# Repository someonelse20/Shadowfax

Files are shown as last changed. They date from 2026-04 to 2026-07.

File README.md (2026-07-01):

# Shadowfax
FPV Drone designed from scrach. This design isn't fully custom yet but will get there eventually. I started this project to make a cool drone and learn as much as I can about engineering.

## Flight Controller
The meat and potatios, the main computer for the drone.
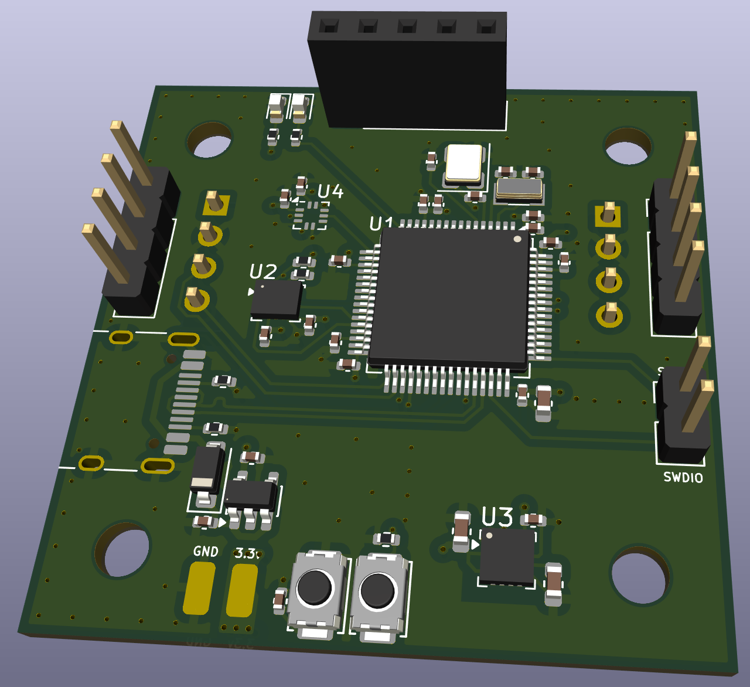
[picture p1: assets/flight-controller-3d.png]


## Transceiver
A low frequency radio to communicate with a remote controller.
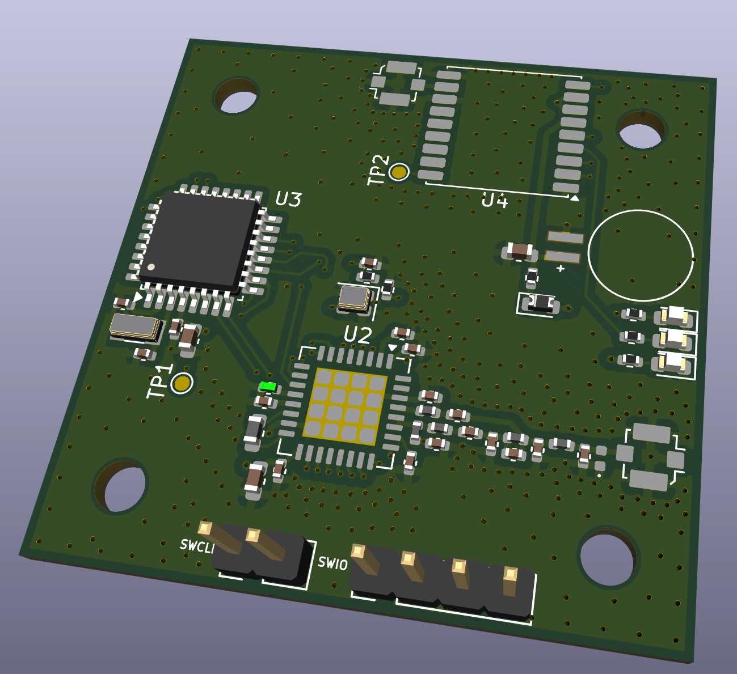
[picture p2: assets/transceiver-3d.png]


## Camera Controller
Controls the camera and captures videos and pictures with a high frequency radio for faster communication.
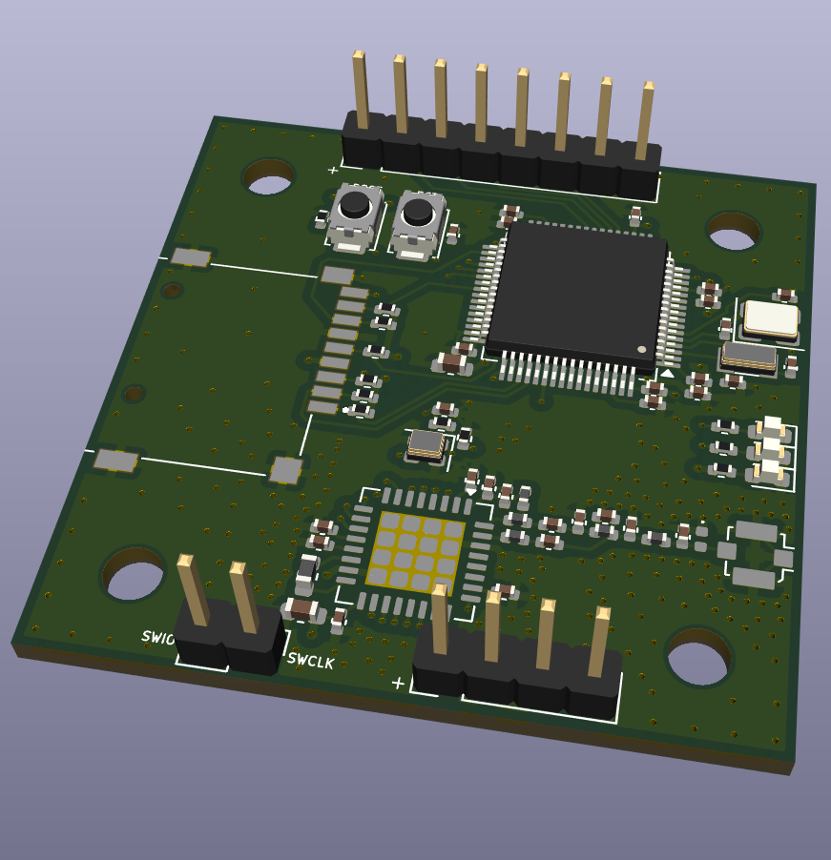
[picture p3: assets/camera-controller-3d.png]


## Power Board
Powers the whole stack with 3.3v and connects the ESCs to the input voltage.
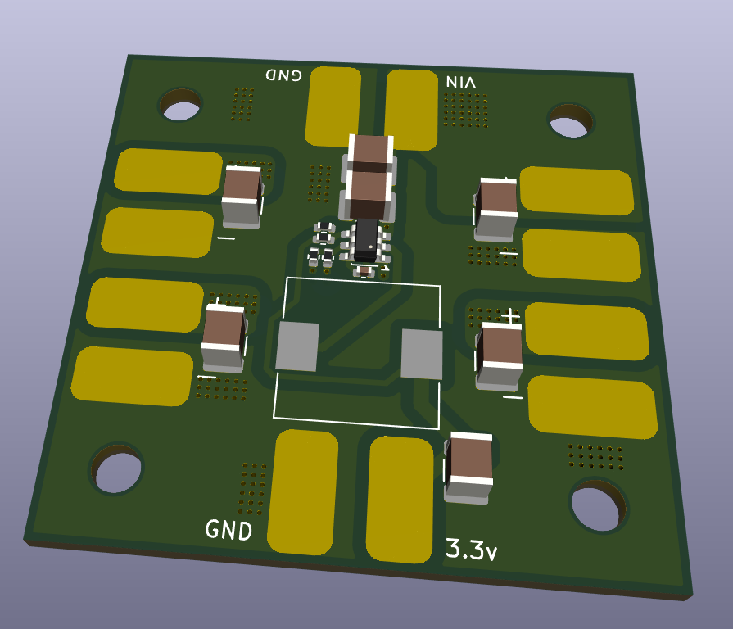
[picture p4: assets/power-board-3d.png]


## Frame
I made a custom frame to fit my custom boards and here it is.
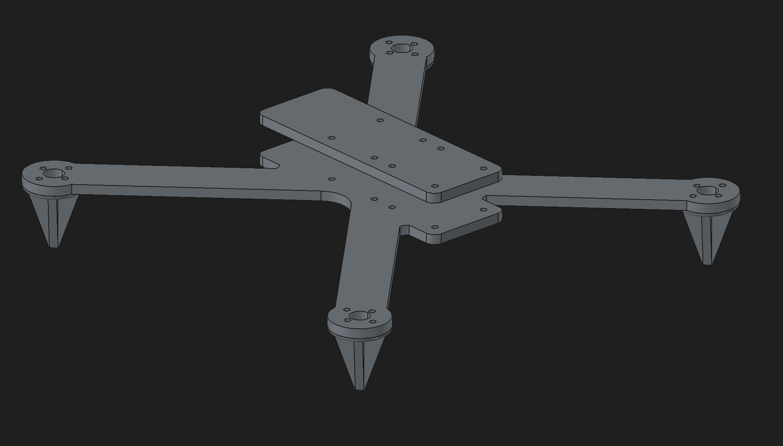
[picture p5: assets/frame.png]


## BOM
| Name | Purpose | Quantity | Total Cost (USD) | Link | Distributor |
|---|---|---|---|---|---|
| Flight Controller Assembly | Assemble components for the flight controller | 2 | 42.44 | https://jlcpcb.com | JLCPCB |
| Flight Controller Board | The pcb for the flight controller | 5 | 2.00 | https://jlcpcb.com | JLCPCB |
| Power Board Assembly | Assemble components for the power board | 2 | 14.79 | https://jlcpcb.com | JLCPCB |
| Power Board | The pcb for the power board | 5 | 7.00 | https://jlcpcb.com | JLCPCB |
| Transceiver Assmebly | Assemble components for the board | 2 | 51.31 | https://jlcpcb.com | JLCPCB |
| Transceiver Board | The pcb for the transceiver | 5 | 7.00 | https://jlcpcb.com | JLCPCB |
| Camera Controller Assembly | Assemble components for the board | 2 | 34.63 | https://jlcpcb.com | JLCPCB |
| Camera Controller Board | The pcb for the camera controller | 5 | 7.00 | https://jlcpcb.com | JLCPCB |

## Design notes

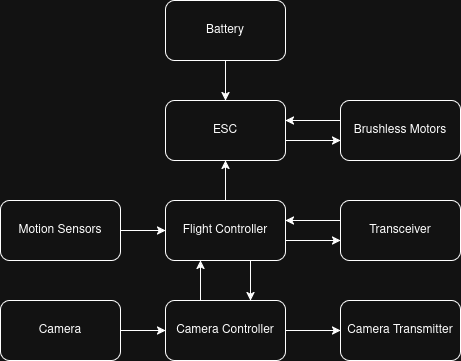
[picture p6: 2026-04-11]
Shadowfax-flowchart.png

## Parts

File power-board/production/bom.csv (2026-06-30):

Designator | Footprint | Quantity | Value | LCSC Part #
C1, C10, C12, C14, C2, C8 | 1210 | 6 | 10uF
C3 | 1210 | 1 | 47uF
C4 | 0402 | 1 | 100nF
J1, J10, J11, J12, J2, J3, J4, J5, J6, J7, J8, J9 | SolderWirePad_1x01_SMD_4x8mm | 12 | Conn_01x01
L1 | L_10.4x10.4_H4.8 | 1 | 10uH
R1, R3 | 0402 | 2 | 100K
R2 | 0402 | 1 | 22K
R4 | 0402 | 1 | 33.2K
U1 | SOT-23-6 | 1 | TPS54308

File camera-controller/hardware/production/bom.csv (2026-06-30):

Designator | Footprint | Quantity | Value | LCSC Part #
BOOT1, RESET1 | SW_Push_SPST_NO_Alps_SKRK | 2 | SW_Push
C10, C13 | 0402 | 2 | 15pF
C11, C18, C20, C24, C25, C27, C29, C31, C32 | 0402 | 9 | 100nF
C12, C14, C9 | 0402 | 3 | 18pF
C19, C21, C34, C36 | 0402 | 4 | 1uF
C2 | 0402 | 1 | 6.8pF
C26, C28, C35, C37 | 0402 | 4 | 2.2uF
C3 | 0402 | 1 | 2.7pF
C30, C33 | 0603 | 2 | 4.7uF
C38 | 0402 | 1 | 1nF
C4 | 0402 | 1 | 1.1pF
C5 | 0402 | 1 | 1.2pF
C6 | 0402 | 1 | 2pF
C7 | 0402 | 1 | 47pF
D1 | 0402 | 1 | D_TVS
D3, D4, D5 | 0603 | 3 | LED
J2 | U.FL_Molex_MCRF_73412-0110_Vertical | 1 | Conn_Coaxial
J3 | PinHeader_1x04_P2.54mm_Vertical | 1 | Conn_01x04
J4 | PinHeader_1x08_P2.54mm_Vertical | 1 | Conn_01x08
J5 | CUI_MSD-4-A | 1 | Micro_SD_Card_Det1
J6 | PinHeader_1x02_P2.54mm_Vertical | 1 | Conn_01x02
L1 | 0603 | 1 | 2.2uH
L2 | 0402 | 1 | 18nH
L3 | 0402 | 1 | 1.5nH
L4 | 0402 | 1 | 1.6nH
L5 | 0402 | 1 | 1.1nH
L7 | 0402 | 1 | 2.4nH
R10, R3, R5, R6, R7, R8, R9 | 0402 | 7 | 10K
R11, R12, R13 | 0402 | 3 | 1.2K
R4 | 0402 | 1 | 120K
TH1 | 0402 | 1 | ERT-J0ER104F
U1 | LQFP-64_10x10mm_P0.5mm | 1 | STM32H523RCTx
U2 | QFN-32-1EP_7x7mm_P0.65mm_EP4.65x4.65mm | 1 | LR2021
Y1 | Crystal_SMD_3215-2Pin_3.2x1.5mm | 1 | 32.768MHz
Y2 | Crystal_SMD_3225-4Pin_3.2x2.5mm | 1 | 24MHz
Y3 | Crystal_SMD_2016-4Pin_2.0x1.6mm | 1 | 32MHz 10pF

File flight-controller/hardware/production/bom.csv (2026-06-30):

Designator | Footprint | Quantity | Value | LCSC Part #
BOOT1, RESET1 | SW_Push_SPST_NO_Alps_SKRK | 2 | SW_Push
C1 | 0603 | 1 | 1uF
C10, C13 | 0402 | 2 | 15pF
C11, C12, C18, C20, C24, C25, C27, C29, C4, C6, C7, C8 | 0402 | 12 | 100nF
C14, C9 | 0402 | 2 | 18pF
C19, C21, C22, C23 | 0402 | 4 | 1uF
C26, C28 | 0402 | 2 | 2.2uF
C30 | 0603 | 1 | 4.7uF
C5 | 0603 | 1 | 10uF
D1, D2 | 0603 | 2 | LED
D3 | D_SOD-123 | 1 | D_Schottky
J1 | USB_C_Receptacle_HRO_TYPE-C-31-M-12 | 1 | USB_C_Receptacle_USB2.0_14P
J2, J3, J4, J5 | PinHeader_1x04_P2.54mm_Vertical | 4 | Conn_01x04
J6 | PinSocket_1x05_P2.54mm_Vertical | 1 | Conn_01x05
J7 | PinHeader_1x02_P2.54mm_Vertical | 1 | Conn_01x02
J8, J9 | SolderWirePad_1x01_SMD_1.5x3mm | 2 | Conn_01x01
R1, R2 | 0402 | 2 | 5.1K
R13, R15 | 0402 | 2 | 1K
R3 | 0402 | 1 | 10K
R4, R5 | 0402 | 2 | 1.2K
U1 | LQFP-64_10x10mm_P0.5mm | 1 | STM32H523RCTx
U2 | LGA-14_3x2.5mm_P0.5mm_LayoutBorder3x4y | 1 | LSM6DSV
U3 | LGA-16_3x3mm_P0.5mm | 1 | MMC5983MA
U4 | Rohm_MLGA010V020A_LGA-10_2x2mm_P0.45mm_LayoutBorder2x3y | 1 | BMP384
U5 | SOT-23-5 | 1 | MIC5504-3.3YM5
Y1 | Crystal_SMD_3215-2Pin_3.2x1.5mm | 1 | 32.768MHz
Y2 | Crystal_SMD_3225-4Pin_3.2x2.5mm | 1 | 24MHz

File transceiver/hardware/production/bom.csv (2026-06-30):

Designator | Footprint | Quantity | Value | LCSC Part #
BT1 | BAT_MS621FE-FL11E | 1 | MS621FE-FL11E
C10 | 0402 | 1 | 7.5pF
C11, C15 | 0402 | 2 | 1.8pF
C13 | 0402 | 1 | 18pF
C14 | 0402 | 1 | 3.9pF
C16 | 0402 | 1 | 2.2pF
C17 | 0603 | 1 | 1uF
C18, C31, C32 | 0402 | 3 | 100nF
C19, C33 | 0603 | 2 | 4.7uF
C22, C23, C8 | 0402 | 3 | 47pF
C34, C36 | 0402 | 2 | 1uF
C35, C37 | 0402 | 2 | 2.2uF
C38 | 0402 | 1 | 1nF
C9 | 0402 | 1 | 22pF
D2 | 0402 | 1 | D_TVS
D3 | 0603 | 1 | D_Schottky
D4, D5, D6 | 0603 | 3 | LED
J2, J5 | U.FL_Molex_MCRF_73412-0110_Vertical | 2 | Conn_Coaxial
J3 | PinHeader_1x04_P2.54mm_Vertical | 1 | Conn_01x04
J4 | PinHeader_1x02_P2.54mm_Vertical | 1 | Conn_01x02
L1 | 0603 | 1 | 2.2uH
L10 | 0402 | 1 | 3.9nH
L11 | 0402 | 1 | 7.5nH
L6 | 0402 | 1 | 12nH
L8 | 0402 | 1 | 4.7nH
L9 | 0402 | 1 | 24nH
R11, R12, R13 | 0402 | 3 | 1.2K
R3 | 0402 | 1 | 1K
R4 | 0402 | 1 | 120K
TH1 | 0402 | 1 | ERT-J0ER104F
TP1, TP2 | TestPoint_Pad_D1.0mm | 2 | TestPoint
U2 | QFN-32-1EP_7x7mm_P0.65mm_EP4.65x4.65mm | 1 | LR2021
U3 | LQFP-32_7x7mm_P0.8mm | 1 | STM32G030K8Tx
U4 | ublox_MAX | 1 | MAX-M10S
Y1 | Crystal_SMD_3215-2Pin_3.2x1.5mm | 1 | 32.768KHz
Y3 | Crystal_SMD_2016-4Pin_2.0x1.6mm | 1 | 32MHz 10pF

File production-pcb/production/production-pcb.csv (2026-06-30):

 | Sourced | Placed | References | Value | Footprint | Quantity
1 |  |  | C4, C6, C7, C8, C11, C12, C18, C20, C24, C25, C27, C29, C32, C40, C42, C43, C45, C46, C47, C48, C50, C53, C65, C69, C70 | 100nF | C_0402_1005Metric | 25
2 |  |  | C19, C21, C22, C23, C41, C44, C61, C63, C75, C76 | 1uF | C_0402_1005Metric | 10
3 |  |  | C26, C28, C38, C39, C58, C60, C72, C73 | 2.2uF | C_0402_1005Metric | 8
4 |  |  | C2, C3, C15, C16, C17, C31 | 10uF | C_1210_3225Metric | 6
5 |  |  | C9, C14, C34, C37, C57, C83 | 18pF | C_0402_1005Metric | 6
6 |  |  | C30, C49, C55, C66, C71 | 4.7uF | C_0603_1608Metric | 5
7 |  |  | C10, C13, C35, C36 | 15pF | C_0402_1005Metric | 4
8 |  |  | C51, C67, C68, C78 | 47pF | C_0402_1005Metric | 4
9 |  |  | C1, C74 | 1uF | C_0603_1608Metric | 2
10 |  |  | C64, C77 | 1nF | C_0402_1005Metric | 2
11 |  |  | C82, C85 | 1.8pF | C_0402_1005Metric | 2
12 |  |  | C5 | 10uF | C_0603_1608Metric | 1
13 |  |  | C33 | 47uF | C_1210_3225Metric | 1
14 |  |  | C52 | 6.8pF | C_0402_1005Metric | 1
15 |  |  | C54 | 2.7pF | C_0402_1005Metric | 1
16 |  |  | C56 | 1.1pF | C_0402_1005Metric | 1
17 |  |  | C59 | 1.2pF | C_0402_1005Metric | 1
18 |  |  | C62 | 2pF | C_0402_1005Metric | 1
19 |  |  | C79 | 22pF | C_0402_1005Metric | 1
20 |  |  | C80 | 2.2pF | C_0402_1005Metric | 1
21 |  |  | C81 | 7.5pF | C_0402_1005Metric | 1
22 |  |  | C84 | 3.9pF | C_0402_1005Metric | 1
23 |  |  | R3, R10, R11, R12, R14, R16, R17, R21 | 10K | R_0402_1005Metric | 8
24 |  |  | R4, R5, R18, R19, R20, R25, R26, R27 | 1.2K | R_0402_1005Metric | 8
25 |  |  | R13, R15, R24 | 1K | R_0402_1005Metric | 3
26 |  |  | R1, R2 | 5.1K | R_0402_1005Metric | 2
27 |  |  | R6, R8 | 100K | R_0402_1005Metric | 2
28 |  |  | R22, R23 | 120K | R_0402_1005Metric | 2
29 |  |  | R7 | 33.2K | R_0402_1005Metric | 1
30 |  |  | R9 | 22K | R_0402_1005Metric | 1
31 |  |  | L6, L8 | 2.2uH | L_0603_1608Metric | 2
32 |  |  | L1 | 10uH | L_10.4x10.4_H4.8 | 1
33 |  |  | L2 | 18nH | L_0402_1005Metric | 1
34 |  |  | L3 | 1.5nH | L_0402_1005Metric | 1
35 |  |  | L4 | 1.6nH | L_0402_1005Metric | 1
36 |  |  | L5 | 1.1nH | L_0402_1005Metric | 1
37 |  |  | L7 | 2.4nH | L_0402_1005Metric | 1
38 |  |  | L9 | 12nH | L_0402_1005Metric | 1
39 |  |  | L10 | 4.7nH | L_0402_1005Metric | 1
40 |  |  | L11 | 24nH | L_0402_1005Metric | 1
41 |  |  | L12 | 3.9nH | L_0402_1005Metric | 1
42 |  |  | L13 | 7.5nH | L_0402_1005Metric | 1
43 |  |  | D1, D2, D4, D5, D6, D9, D10, D11 | LED | LED_0603_1608Metric | 8
44 |  |  | D7, D12 | D_TVS | D_0402_1005Metric | 2
45 |  |  | D3 | D_Schottky | D_SOD-123 | 1
46 |  |  | D8 | D_Schottky | D_0603_1608Metric | 1
47 |  |  | U1, U7 | STM32H523RCTx | LQFP-64_10x10mm_P0.5mm | 2
48 |  |  | U8, U11 | LR2021 | QFN-32-1EP_7x7mm_P0.65mm_EP4.65x4.65mm | 2
49 |  |  | U2 | LSM6DSV | LGA-14_3x2.5mm_P0.5mm_LayoutBorder3x4y | 1
50 |  |  | U3 | MMC5983MA | LGA-16_3x3mm_P0.5mm | 1
51 |  |  | U4 | BMP384 | Rohm_MLGA010V020A_LGA-10_2x2mm_P0.45mm_LayoutBorder2x3y | 1
52 |  |  | U5 | MIC5504-3.3YM5 | SOT-23-5 | 1
53 |  |  | U6 | TPS54308 | SOT-23-6 | 1
54 |  |  | U9 | STM32G030K8Tx | LQFP-32_7x7mm_P0.8mm | 1
55 |  |  | U10 | MAX-M10S | ublox_MAX | 1
56 |  |  | Y1, Y3 | 32.768MHz | Crystal_SMD_3215-2Pin_3.2x1.5mm | 2
57 |  |  | Y2, Y4 | 24MHz | Crystal_SMD_3225-4Pin_3.2x2.5mm | 2
58 |  |  | Y5, Y7 | 32MHz 10pF | Crystal_SMD_2016-4Pin_2.0x1.6mm | 2
59 |  |  | Y6 | 32.768KHz | Crystal_SMD_3215-2Pin_3.2x1.5mm | 1
60 |  |  | BOOT1, BOOT2, RESET1, RESET2 | SW_Push | SW_Push_SPST_NO_Alps_SKRK | 4
61 |  |  | TH1, TH2 | ERT-J0ER104F | R_0402_1005Metric | 2
62 |  |  | TP1, TP2 | TestPoint | TestPoint_Pad_D1.0mm | 2
63 |  |  | BT1 | MS621FE-FL11E | BAT_MS621FE-FL11E | 1
64 |  |  | J10, J11, J12, J13, J14, J15, J16, J17, J18, J19, J20, J21 | Conn_01x01 | SolderWirePad_1x01_SMD_4x8mm | 12
65 |  |  | J2, J3, J5, J22 | Conn_01x04 | PinHeader_1x04_P2.54mm_Vertical | 4
66 |  |  | J4, J7, J24 | Conn_01x02 | PinHeader_1x02_P2.54mm_Vertical | 3
67 |  |  | J26, J29, J30 | Conn_Coaxial | U.FL_Molex_MCRF_73412-0110_Vertical | 3
68 |  |  | J8, J9 | Conn_01x01 | SolderWirePad_1x01_SMD_1.5x3mm | 2
69 |  |  | J1 | USB_C_Receptacle_USB2.0_14P | USB_C_Receptacle_HRO_TYPE-C-31-M-12 | 1
70 |  |  | J6 | Conn_01x05 | PinSocket_1x05_P2.54mm_Vertical | 1
71 |  |  | J23 | Conn_01x08 | PinHeader_1x08_P2.54mm_Vertical | 1
72 |  |  | J25 | Micro_SD_Card_Det1 | CUI_MSD-4-A | 1

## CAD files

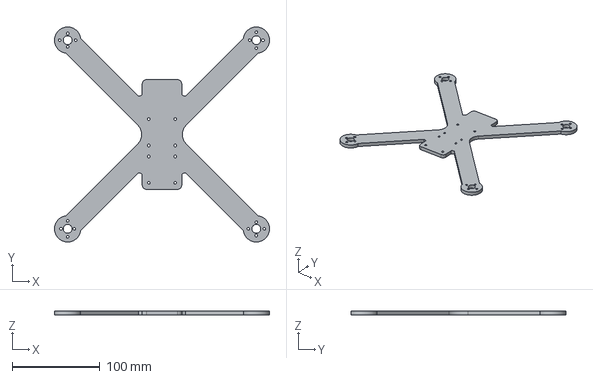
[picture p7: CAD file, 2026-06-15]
frame/exports/frame-Body.step
244.7 x 244.7 x 5.00 mm

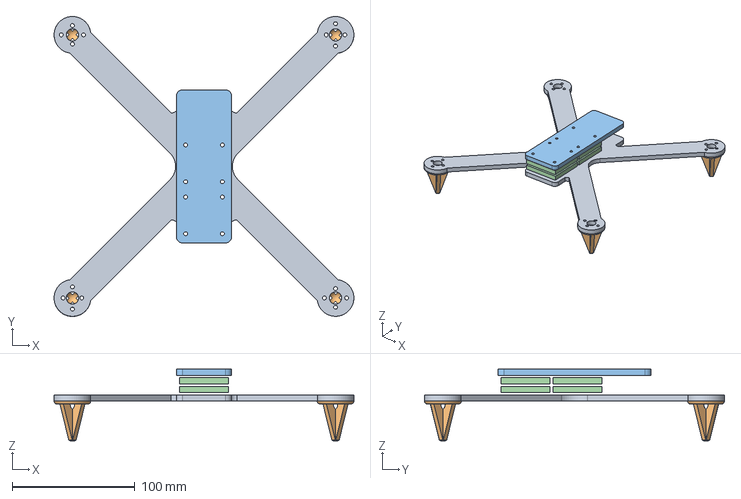
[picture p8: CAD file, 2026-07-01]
model.step
244.7 x 244.8 x 58.5 mm

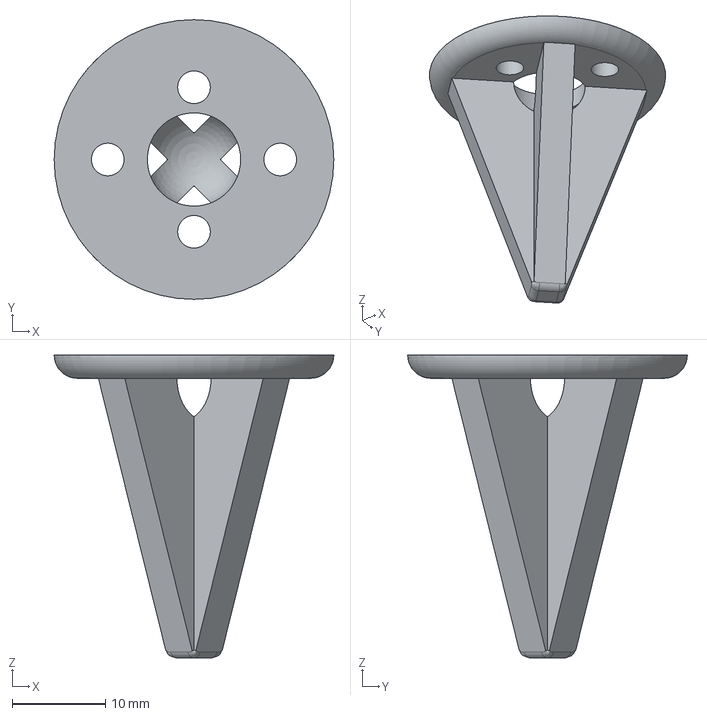
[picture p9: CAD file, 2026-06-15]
frame/exports/feet-Body.step
30.0 x 30.0 x 32.5 mm

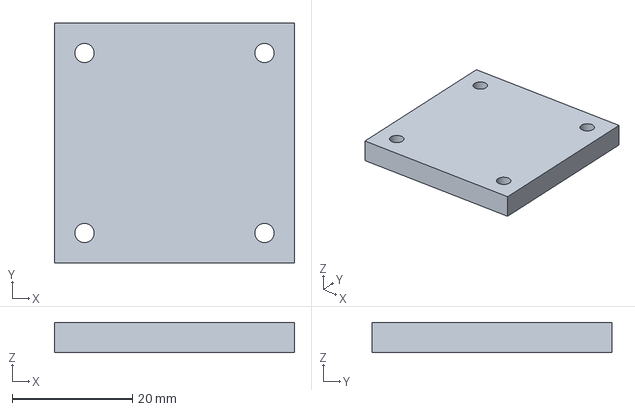
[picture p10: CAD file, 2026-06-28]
frame/board_model.FCStd
40.0 x 40.0 x 5.00 mm

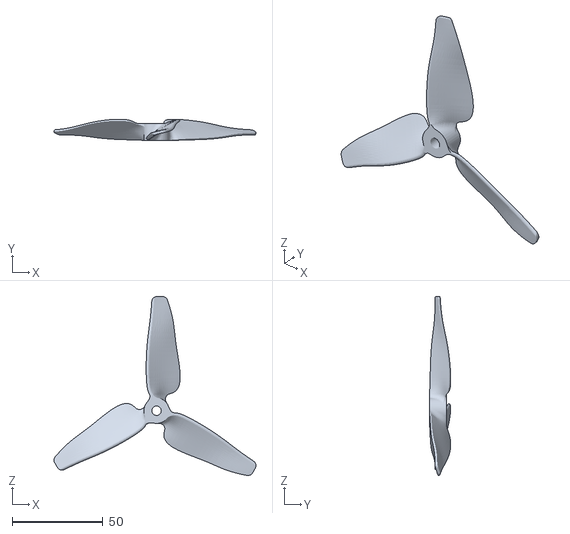
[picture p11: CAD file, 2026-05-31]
frame/Propeller_5_inch (1).stl
111.4 x 11.8 x 98.7

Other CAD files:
frame/assembly.FCStd
frame/feet.FCStd
frame/frame.FCStd
frame/sketch.FCStd
frame/exports/feet-Body.3mf

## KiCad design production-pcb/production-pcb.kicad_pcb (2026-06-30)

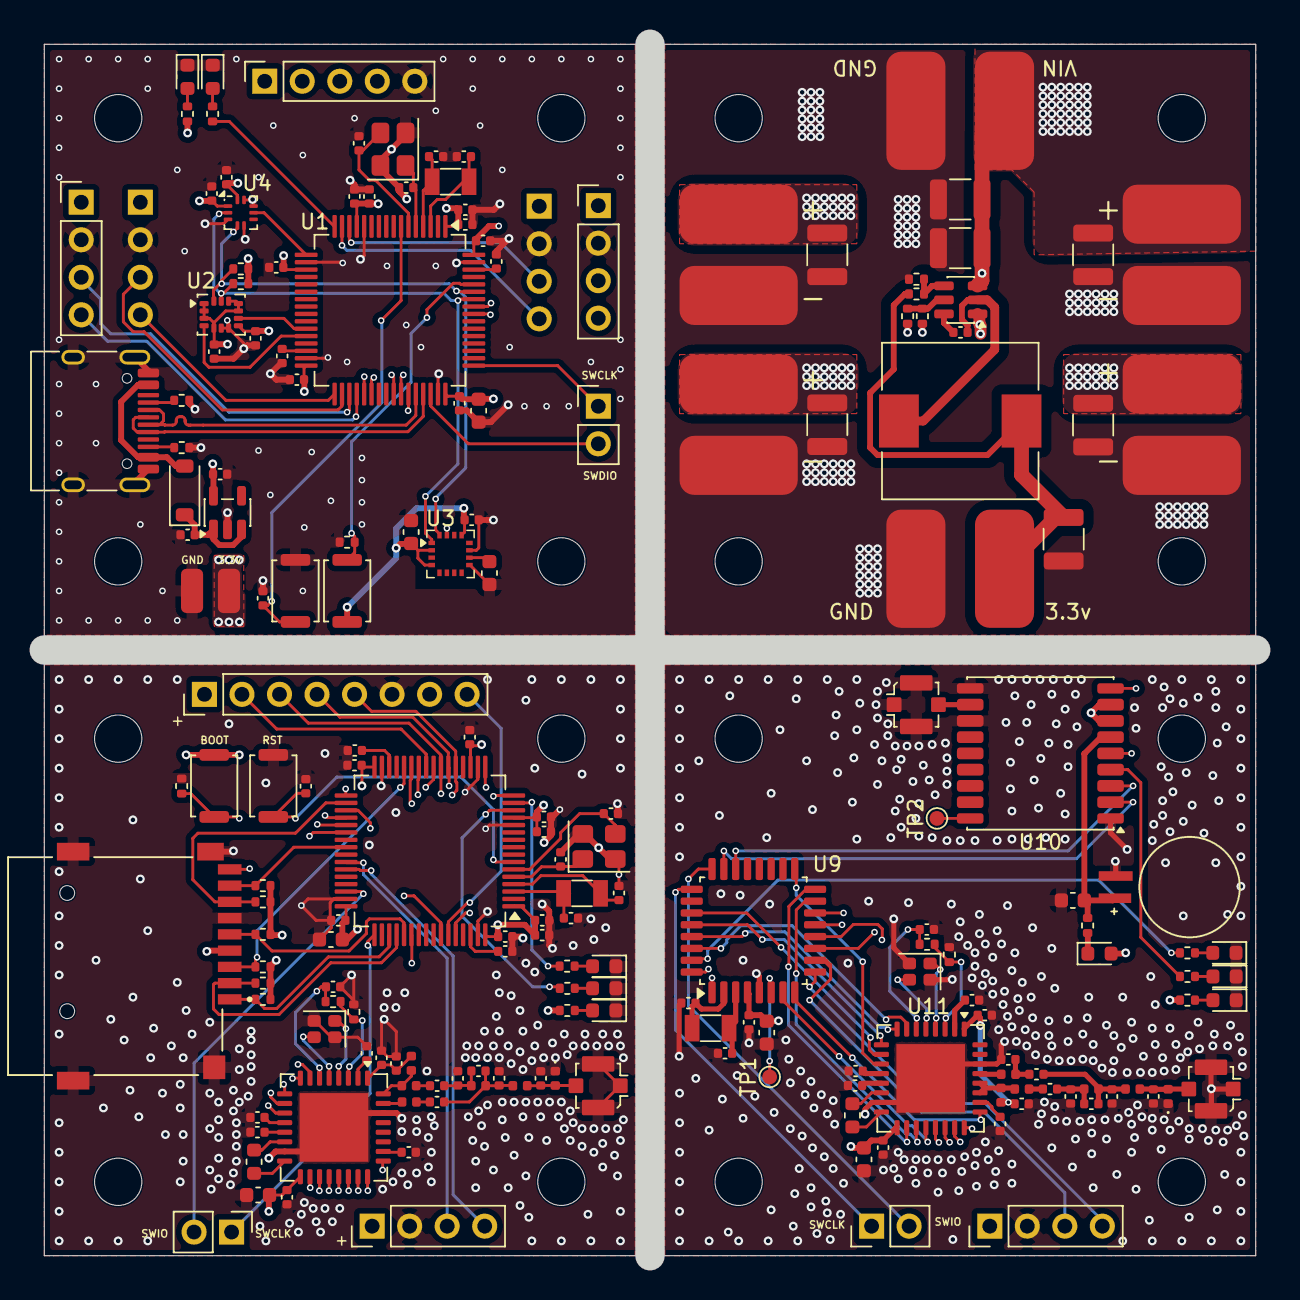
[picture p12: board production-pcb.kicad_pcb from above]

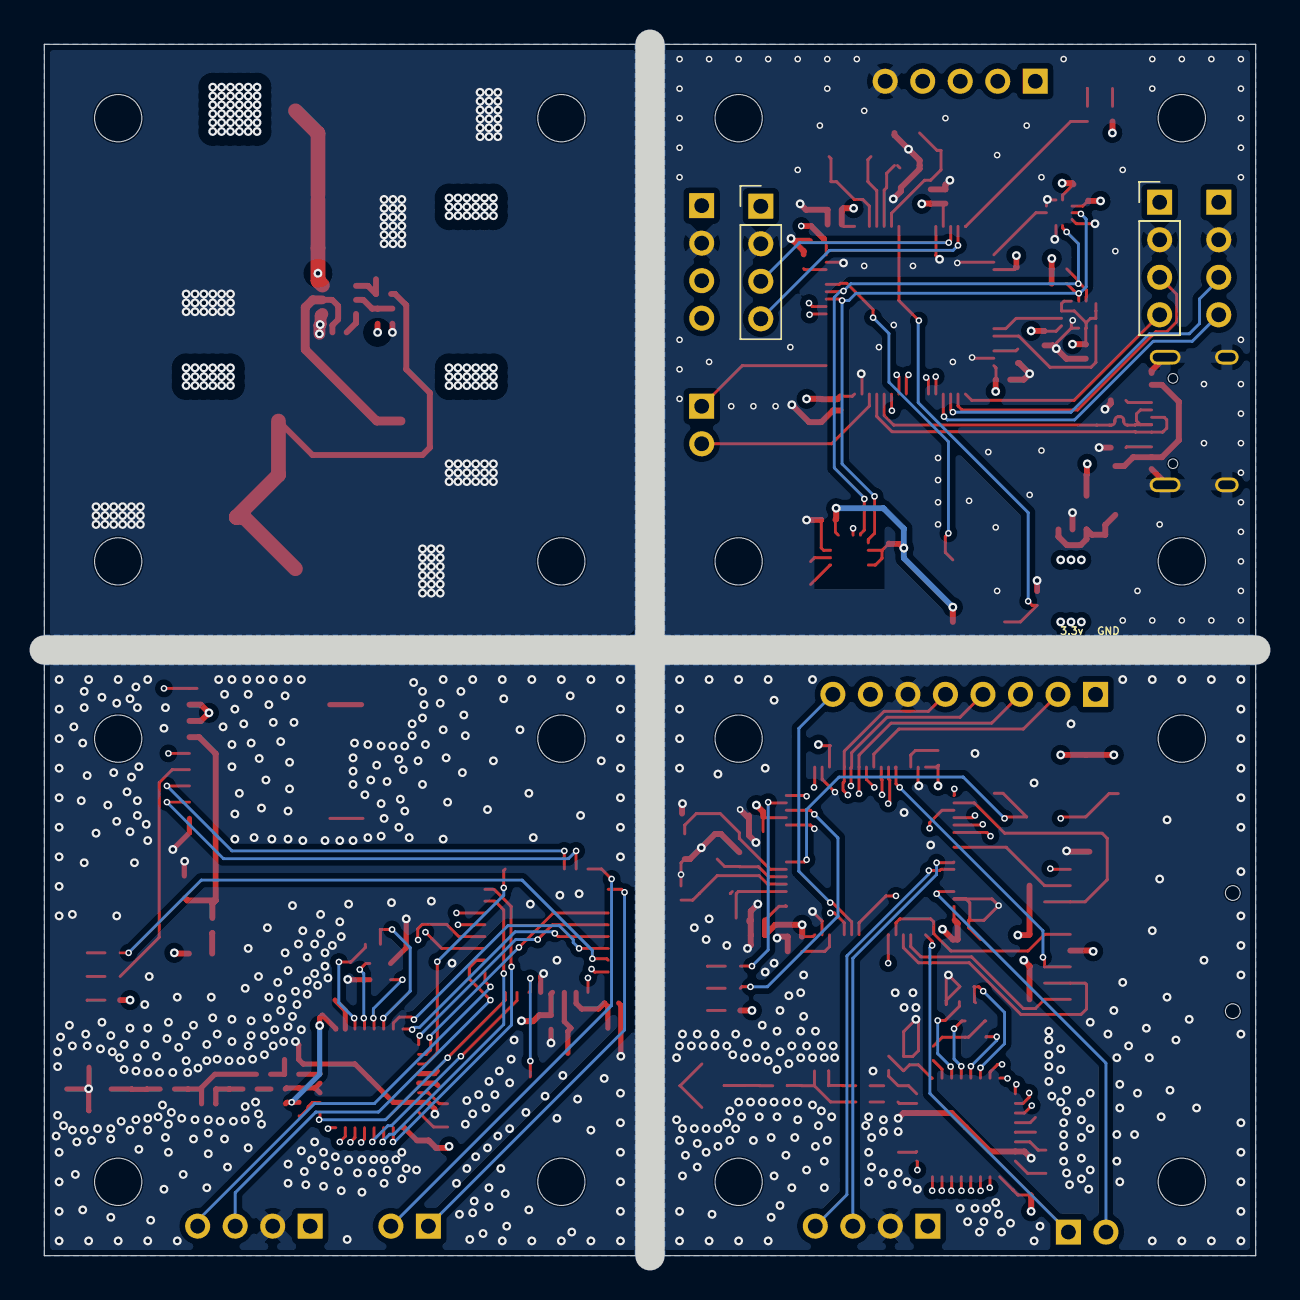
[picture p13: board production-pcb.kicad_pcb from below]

Board: 4 copper layers, 82.0 x 82.0 mm, 194 parts (2 on the bottom side), 109 nets.

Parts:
BOOT1, BOOT2: SW_Push; SW_Push_SPST_NO_Alps_SKRK
BT1: MS621FE-FL11E; BAT_MS621FE-FL11E
C1, C74: 1uF; C_0603_1608Metric
C2, C3, C15, C16, C17, C31: 10uF; C_1210_3225Metric
C4, C6, C7, C8, C11, C12, C18, C20, C24, C25, C27, C29, C32, C40, C42, C43, C45, C46, C47, C48, C50, C53, C65, C69, C70: 100nF; C_0402_1005Metric
C5: 10uF; C_0603_1608Metric
C9, C14, C34, C37, C57, C83: 18pF; C_0402_1005Metric
C10, C13, C35, C36: 15pF; C_0402_1005Metric
C19, C21, C22, C23, C41, C44, C61, C63, C75, C76: 1uF; C_0402_1005Metric
C26, C28, C38, C39, C58, C60, C72, C73: 2.2uF; C_0402_1005Metric
C30, C49, C55, C66, C71: 4.7uF; C_0603_1608Metric
C33: 47uF; C_1210_3225Metric
C51, C67, C68, C78: 47pF; C_0402_1005Metric
C52: 6.8pF; C_0402_1005Metric
C54: 2.7pF; C_0402_1005Metric
C56: 1.1pF; C_0402_1005Metric
C59: 1.2pF; C_0402_1005Metric
C62: 2pF; C_0402_1005Metric
C64, C77: 1nF; C_0402_1005Metric
C79: 22pF; C_0402_1005Metric
C80: 2.2pF; C_0402_1005Metric
C81: 7.5pF; C_0402_1005Metric
C82, C85: 1.8pF; C_0402_1005Metric
C84: 3.9pF; C_0402_1005Metric
D1, D2, D4, D5, D6, D9, D10, D11: LED; LED_0603_1608Metric
D3: D_Schottky; D_SOD-123
D7, D12: D_TVS; D_0402_1005Metric
D8: D_Schottky; D_0603_1608Metric
J1: USB_C_Receptacle_USB2.0_14P; USB_C_Receptacle_HRO_TYPE-C-31-M-12
J2, J3, J3#2, J4#2, J5, J22: Conn_01x04; PinHeader_1x04_P2.54mm_Vertical
J4, J7, J24: Conn_01x02; PinHeader_1x02_P2.54mm_Vertical
J6: Conn_01x05; PinSocket_1x05_P2.54mm_Vertical
J8, J9: Conn_01x01; SolderWirePad_1x01_SMD_1.5x3mm
J10, J11, J12, J13, J14, J15, J16, J17, J18, J19, J20, J21: Conn_01x01; SolderWirePad_1x01_SMD_4x8mm
J23: Conn_01x08; PinHeader_1x08_P2.54mm_Vertical
J25: Micro_SD_Card_Det1; CUI_MSD-4-A
J26, J29, J30: Conn_Coaxial; U.FL_Molex_MCRF_73412-0110_Vertical
L1: 10uH; L_10.4x10.4_H4.8
L2: 18nH; L_0402_1005Metric
L3: 1.5nH; L_0402_1005Metric
L4: 1.6nH; L_0402_1005Metric
L5: 1.1nH; L_0402_1005Metric
L6, L8: 2.2uH; L_0603_1608Metric
L7: 2.4nH; L_0402_1005Metric
L9: 12nH; L_0402_1005Metric
L10: 4.7nH; L_0402_1005Metric
L11: 24nH; L_0402_1005Metric
L12: 3.9nH; L_0402_1005Metric
L13: 7.5nH; L_0402_1005Metric
R1, R2: 5.1K; R_0402_1005Metric
R3, R10, R11, R12, R14, R16, R17, R21: 10K; R_0402_1005Metric
R4, R5, R18, R19, R20, R25, R26, R27: 1.2K; R_0402_1005Metric
R6, R8: 100K; R_0402_1005Metric
R7: 33.2K; R_0402_1005Metric
R9: 22K; R_0402_1005Metric
R13, R15, R24: 1K; R_0402_1005Metric
R22, R23: 120K; R_0402_1005Metric
RESET1, RESET2: SW_Push; SW_Push_SPST_NO_Alps_SKRK
TH1, TH2: ERT-J0ER104F; R_0402_1005Metric
TP1, TP2: TestPoint; TestPoint_Pad_D1.0mm
U1, U7: STM32H523RCTx; LQFP-64_10x10mm_P0.5mm
U2: LSM6DSV; LGA-14_3x2.5mm_P0.5mm_LayoutBorder3x4y
U3: MMC5983MA; LGA-16_3x3mm_P0.5mm
U4: BMP384; Rohm_MLGA010V020A_LGA-10_2x2mm_P0.45mm_LayoutBorder2x3y
U5: MIC5504-3.3YM5; SOT-23-5
U6: TPS54308; SOT-23-6
U8, U11: LR2021; QFN-32-1EP_7x7mm_P0.65mm_EP4.65x4.65mm
U9: STM32G030K8Tx; LQFP-32_7x7mm_P0.8mm
U10: MAX-M10S; ublox_MAX
Y1, Y3: 32.768MHz; Crystal_SMD_3215-2Pin_3.2x1.5mm
Y2, Y4: 24MHz; Crystal_SMD_3225-4Pin_3.2x2.5mm
Y5, Y7: 32MHz 10pF; Crystal_SMD_2016-4Pin_2.0x1.6mm
Y6: 32.768KHz; Crystal_SMD_3215-2Pin_3.2x1.5mm

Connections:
+3.3V: BOOT1.1, BOOT2.1, C1.1, C4.1, C6.1, C7.1, C8.1, C12.1, C18.1, C19.1, C20.1, C21.1, C23.1, C24.1, C25.1, C27.1, C29.1, C30.1, C40.1, C41.1, C42.1, C44.1, C45.1, C46.1, C47.1, C48.1, C49.1, C53.1, C55.1, C65.1, C66.1, C70.1, C71.1, D8.2 (A), J2.1, J3.1, J3#2.1, J4#2.1, J5.1, J8.1 (Pin_1_1), J22.1, J23.7, J25.4 (VDD), R4.1, R5.1, R10.1, R11.1, R12.1, R14.1, R15.1, R16.1, R17.1, R18.1, R25.1, U1.1 (VBAT), U1.13 (VDDA), U1.19 (VDD), U1.32 (VDD), U1.48 (VDD), U1.64 (VDD), U2.1 (SDO/SA0), U2.2 (SDX), U2.3 (SCX), U2.5 (VDDIO), U2.8 (VDD), U2.10 (OCS_Aux), U2.11 (SDO_Aux), U2.12 (CS), U3.2 (VDD), U3.4 (SPI_CS), U3.13 (VDDIO), U4.1 (VDDIO), U4.10 (VDD), U5.5 (VOUT), U7.1 (VBAT), U7.13 (VDDA), U7.19 (VDD), U7.32 (VDD), U7.48 (VDD), U7.64 (VDD), U8.17 (VBAT), U9.4 (VDD), U10.7 (VCC_IO), U10.8 (VCC), U11.17 (VBAT)
/BMP_INT: U1.17 (PA3), U4.7 (INT)
/BOOT: BOOT1.2, BOOT2.2, R3.1, R21.1, U1.60 (BOOT0), U7.60 (BOOT0)
/CAM_CS: J23.2, U7.25 (PC5)
/CAM_STAT: R19.1, U7.14 (PA0)
/ESC1: J6.1, U1.41 (PA8)
/ESC2: J6.2, U1.42 (PA9)
/ESC3: J6.3, U1.56 (PB4(NJTRST))
/ESC4: J6.4, U1.57 (PB5)
/GPS_INT: U9.32 (PB8), U10.5 (EXTINT)
/GPS_LED: R26.1, U10.4 (TIMEPULSE)
/GPS_RST: U9.1 (PB9), U10.9 (~RESET)
/GPS_RX: U9.23 (PA10/PA12), U10.2 (TXD)
/GPS_TX: U9.22 (PA9/PA11), U10.3 (RXD)
/HSE_IN: C9.1, C37.1, U1.5 (PH0), U7.5 (PH0), Y2.1, Y4.1
/HSE_OUT: C14.1, C34.1, U1.6 (PH1), U7.6 (PH1), Y2.3, Y4.3
/LMS_INT2: U1.27 (PB1), U2.9 (INT2)
/LR_BUSY: U7.16 (PA2), U8.25 (BUSY), U9.8 (PA1), U11.25 (BUSY)
/LR_CS: U7.17 (PA3), U8.24 (NSS)
/LR_D5: U7.26 (PB0), U8.19 (DIO5), U9.15 (PB0), U11.19 (DIO5)
/LR_D6: U7.27 (PB1), U8.18 (DIO6), U9.16 (PB1), U11.18 (DIO6)
/LR_D7: U7.38 (PC7), U8.11 (DIO7), U9.17 (PB2), U11.11 (DIO7)
/LR_D8: U7.37 (PC6), U8.10 (DIO8), U9.27 (PB3), U11.10 (DIO8)
/LR_D9: U7.36 (PB15), U8.9 (DIO9), U9.28 (PB4), U11.9 (DIO9)
/LR_D10: U7.35 (PB14), U8.8 (DIO10), U9.29 (PB5), U11.8 (DIO10)
/LR_D11: U7.33 (PB12), U8.7 (DIO11), U9.30 (PB6), U11.7 (DIO11)
/LR_RST: U7.24 (PC4), U8.20 (~RESET), U9.7 (PA0), U11.20 (~RESET)
/LR_STAT: R20.1, R27.1, U7.15 (PA1), U9.31 (PB7)
/LSE_IN: C10.1, C35.1, C67.2, U1.3 (PC14), U7.3 (PC14), U9.2 (PC14), Y1.1, Y3.1, Y6.2
/LSE_OUT: C13.1, C36.1, C68.2, U1.4 (PC15), U7.4 (PC15), U9.3 (PC15), Y1.2, Y3.2, Y6.1
/LSM_INT1: U1.28 (PB2), U2.4 (INT1)
/MISO: J23.4, U7.22 (PA6), U8.21 (MISO), U9.13 (PA6), U11.21 (MISO)
/MMC_INT: U1.43 (PA10), U3.15 (INT)
/MOSI: J23.3, U7.23 (PA7), U8.22 (MOSI), U9.14 (PA7), U11.22 (MOSI)
/NSS: U9.11 (PA4), U11.24 (NSS)
/NTC: R22.2, R23.2, TH1.1, TH2.1, U8.3 (NTC), U11.3 (NTC)
/RFI: L7.1, U8.31 (RFI_HF)
/RFI_LF: L11.1, U11.29 (RFI_LF)
/RFO: L2.2, L3.1, U8.32 (RFO_HF)
/RFO_LF1: L9.2, L10.1, U11.27 (RFO_LF2), U11.28 (RFO_LF1)
/SCK: J23.5, U7.21 (PA5), U8.23 (SCK), U9.12 (PA5), U11.23 (SCK)
/SCL: J23.1, R4.2, U1.58 (PB6), U2.13 (SCL), U3.1 (SCL/SPI_SCK), U4.2 (SCK), U7.58 (PB6)
/SDA: J23.8, R5.2, U1.59 (PB7), U2.14 (SDA), U3.16 (SDA/SPI_SDI), U4.4 (SDI), U7.59 (PB7)
/SD_CLK: J25.5 (CLK), R14.2, U7.53 (PC12)
/SD_CMD: J25.3 (CMD), R12.2, U7.28 (PB2)
/SD_D0: J25.7 (DAT0), R16.2, U7.34 (PB13)
/SD_D1: J25.8 (DAT1), R17.2, U7.40 (PC9)
/SD_D2: J25.1 (DAT2), R10.2, U7.51 (PC10)
/SD_D3: J25.2 (DAT3/CD), R11.2, U7.52 (PC11)
/SD_DET: J25.9 (DET), U7.54 (PD2)
/STAT_LED: R13.1, U1.16 (PA2)
/STM32_RST: C11.2, C43.2, RESET1.2, RESET2.2, U1.7 (NRST), U7.7 (NRST)
/SWCLK: J4.1, J7.1, J24.1, U1.49 (PA14(JTCK), U7.49 (PA14(JTCK), U9.25 (PA14)
/SWDIO: J4.2, J7.2, J24.2, U1.46 (PA13(JTMS), U7.46 (PA13(JTMS), U9.24 (PA13)
/UART_RX: J3.3, J22.3, U7.42 (PA9), U9.10 (PA3)
/UART_RX1: J2.4, U1.36 (PB15)
/UART_RX4: J4#2.4, U1.15 (PA1)
/UART_RX5: J3#2.4, U1.33 (PB12)
/UART_RX6: J5.4, U1.38 (PC7)
/UART_TX: J3.4, J22.4, U7.43 (PA10), U9.9 (PA2)
/UART_TX1: J2.3, U1.35 (PB14)
/UART_TX4: J4#2.3, U1.14 (PA0)
/UART_TX5: J3#2.3, U1.34 (PB13)
/UART_TX6: J5.3, U1.37 (PC6)
/USB_+: J1.A6 (D+), J1.B6 (D+), U1.45 (PA12), U7.45 (PA12)
/USB_-: J1.A7 (D-), J1.B7 (D-), U1.44 (PA11), U7.44 (PA11)
/VDCC1: C63.1, C76.1, U8.12 (VDCC1), U11.12 (VDCC1)
/VDCC2: C61.1, C75.1, U8.26 (VDCC2), U11.26 (VDCC2)
/VNTC: C50.1, C69.1, R22.1, R23.1, U8.6 (VTCXO/VNTC), U11.6 (VTCXO/VNTC)
/VPAX1: C60.1, C73.1, U8.13 (VPAX1), U11.13 (VPAX1)
/VPAX2: C58.1, C72.1, U8.2 (VPAX2), U11.2 (VPAX2)
/VR_PA: C51.1, C64.1, C77.1, C78.1, L2.1, L9.1, U8.1 (VR_PA), U11.1 (VR_PA)
/V_BCKP: BT1.1 (+), C74.1, R24.2, U10.6 (V_BCKP)
GND: BT1.2 (-), C1.2, C2.2, C3.2, C4.2, C5.2, C6.2, C7.2, C8.2, C9.2, C10.2, C11.1, C12.2, C13.2, C14.2, C15.2, C16.2, C17.2, C18.2, C19.2, C20.2, C21.2, C22.2, C23.2, C24.2, C25.2, C26.2, C27.2, C28.2, C29.2, C30.2, C31.2, C33.2, C34.2, C35.2, C36.2, C37.2, C38.2, C39.2, C40.2, C41.2, C42.2, C43.1, C44.2, C45.2, C46.2, C47.2, C48.2, C49.2, C50.2, C51.2, C53.2, C54.2, C55.2, C58.2, C59.2, C60.2, C61.2, C62.2, C63.2, C64.2, C65.2, C66.2, C67.1, C68.1, C69.2, C70.2, C71.2, C72.2, C73.2, C74.2, C75.2, C76.2, C77.2, C78.2, C80.2, C81.2, C84.2, C85.2, D1.1 (K), D2.1 (K), D4.1 (K), D5.1 (K), D6.1 (K), D7.1 (A1), D9.1 (K), D10.1 (K), D11.1 (K), D12.1 (A1), J1.A1 (GND), J1.A12 (GND), J1.B1 (GND), J1.B12 (GND), J1.SH (SHIELD), J2.2, J3.2, J3#2.2, J4#2.2, J5.2, J6.5, J9.1 (Pin_1_1), J11.1 (Pin_1_1), J13.1 (Pin_1_1), J15.1 (Pin_1_1), J17.1 (Pin_1_1), J19.1 (Pin_1_1), J21.1 (Pin_1_1), J22.2, J23.6, J25.6 (VSS), J25.SH (SHIELD), J26.2 (Ext), J29.2 (Ext), J30.2 (Ext), R1.2, R2.1, R3.2, R7.2, R9.2, R21.2, RESET1.1, RESET2.1, TH1.2, TH2.2, U1.12 (VSSA), U1.18 (VSS), U1.31 (VSS), U1.47 (VSS), U1.63 (VSS), U2.6 (GND), U2.7 (GND), U3.9 (GND), U3.11 (GND), U4.3 (VSS), U4.5 (SDO), U4.8 (VSS), U4.9 (VSS), U5.2 (GND), U6.1 (GND), U7.12 (VSSA), U7.18 (VSS), U7.31 (VSS), U7.47 (VSS), U7.63 (VSS), U8.15 (GND_DCC), U8.30 (GND), U8.33 (GND), U9.5 (VSS), U10.1 (GND), U10.10 (GND), U10.12 (GND), U11.15 (GND_DCC), U11.30 (GND), U11.33 (GND), Y2.2, Y2.4, Y4.2, Y4.4, Y5.2 (G), Y5.4 (G), Y7.2 (G), Y7.4 (G)
unnamed: C52.1, L3.2
unnamed: C52.2, C54.1, C56.1, L4.2
unnamed: C79.1, L10.2
unnamed: C79.2, C81.1, C82.1, L12.2
unnamed: C82.2, C83.2, C84.1, L12.1, L13.1
unnamed: C57.1, L7.2
unnamed: C56.2, C57.2, C59.1, L4.1, L5.1
unnamed: C80.1, C83.1, L11.2
unnamed: C26.1, C39.1, U1.62 (VCAP), U7.62 (VCAP)
unnamed: C28.1, C38.1, U1.30 (VCAP), U7.30 (VCAP)
unnamed: C62.1, D7.2 (A2), J26.1 (In), L5.2
unnamed: D1.2 (A), R15.2
unnamed: C85.1, D12.2 (A2), J30.1 (In), L13.2
unnamed: D2.2 (A), R13.2
unnamed: D3.2 (A), D4.2 (A), J1.A4 (VBUS), J1.A9 (VBUS), J1.B4 (VBUS), J1.B9 (VBUS), R18.2
unnamed: C22.1, D3.1 (K), D8.1 (K), R24.1, U5.1 (VIN), U5.3 (EN)
unnamed: D5.2 (A), D9.2 (A), R19.2, R25.2
unnamed: D6.2 (A), D10.2 (A), R20.2, R26.2
unnamed: D11.2 (A), R27.2
unnamed: J1.A5 (CC1), R1.1
unnamed: J1.B5 (CC2), R2.2
unnamed: C33.1, J20.1 (Pin_1_1), L1.2, R8.1
unnamed: J29.1 (In), U10.11 (RF_IN)
unnamed: C32.1, U6.6 (BOOT)
unnamed: R6.2, R7.1, U6.5 (EN)
unnamed: R8.2, R9.1, U6.4 (FB)
unnamed: C32.2, L1.1, U6.2 (SW)
unnamed: L6.1, L8.1, U8.16 (LXA), U11.16 (LXA)
unnamed: L6.2, L8.2, U8.14 (LXB), U11.14 (LXB)
unnamed: U8.4 (XTA), U11.4 (XTA), Y5.1, Y7.1
unnamed: U8.5 (XTB), U11.5 (XTB), Y5.3, Y7.3
unnamed: C5.1, U3.10 (CAP)
unnamed: TP1.1 (1_1), U9.6 (NRST)
unnamed: TP2.1 (1_1), U10.18 (~SAFEBOOT)
VBUS: C2.1, C3.1, C15.1, C16.1, C17.1, C31.1, J10.1 (Pin_1_1), J12.1 (Pin_1_1), J14.1 (Pin_1_1), J16.1 (Pin_1_1), J18.1 (Pin_1_1), R6.1, U6.3 (VIN)

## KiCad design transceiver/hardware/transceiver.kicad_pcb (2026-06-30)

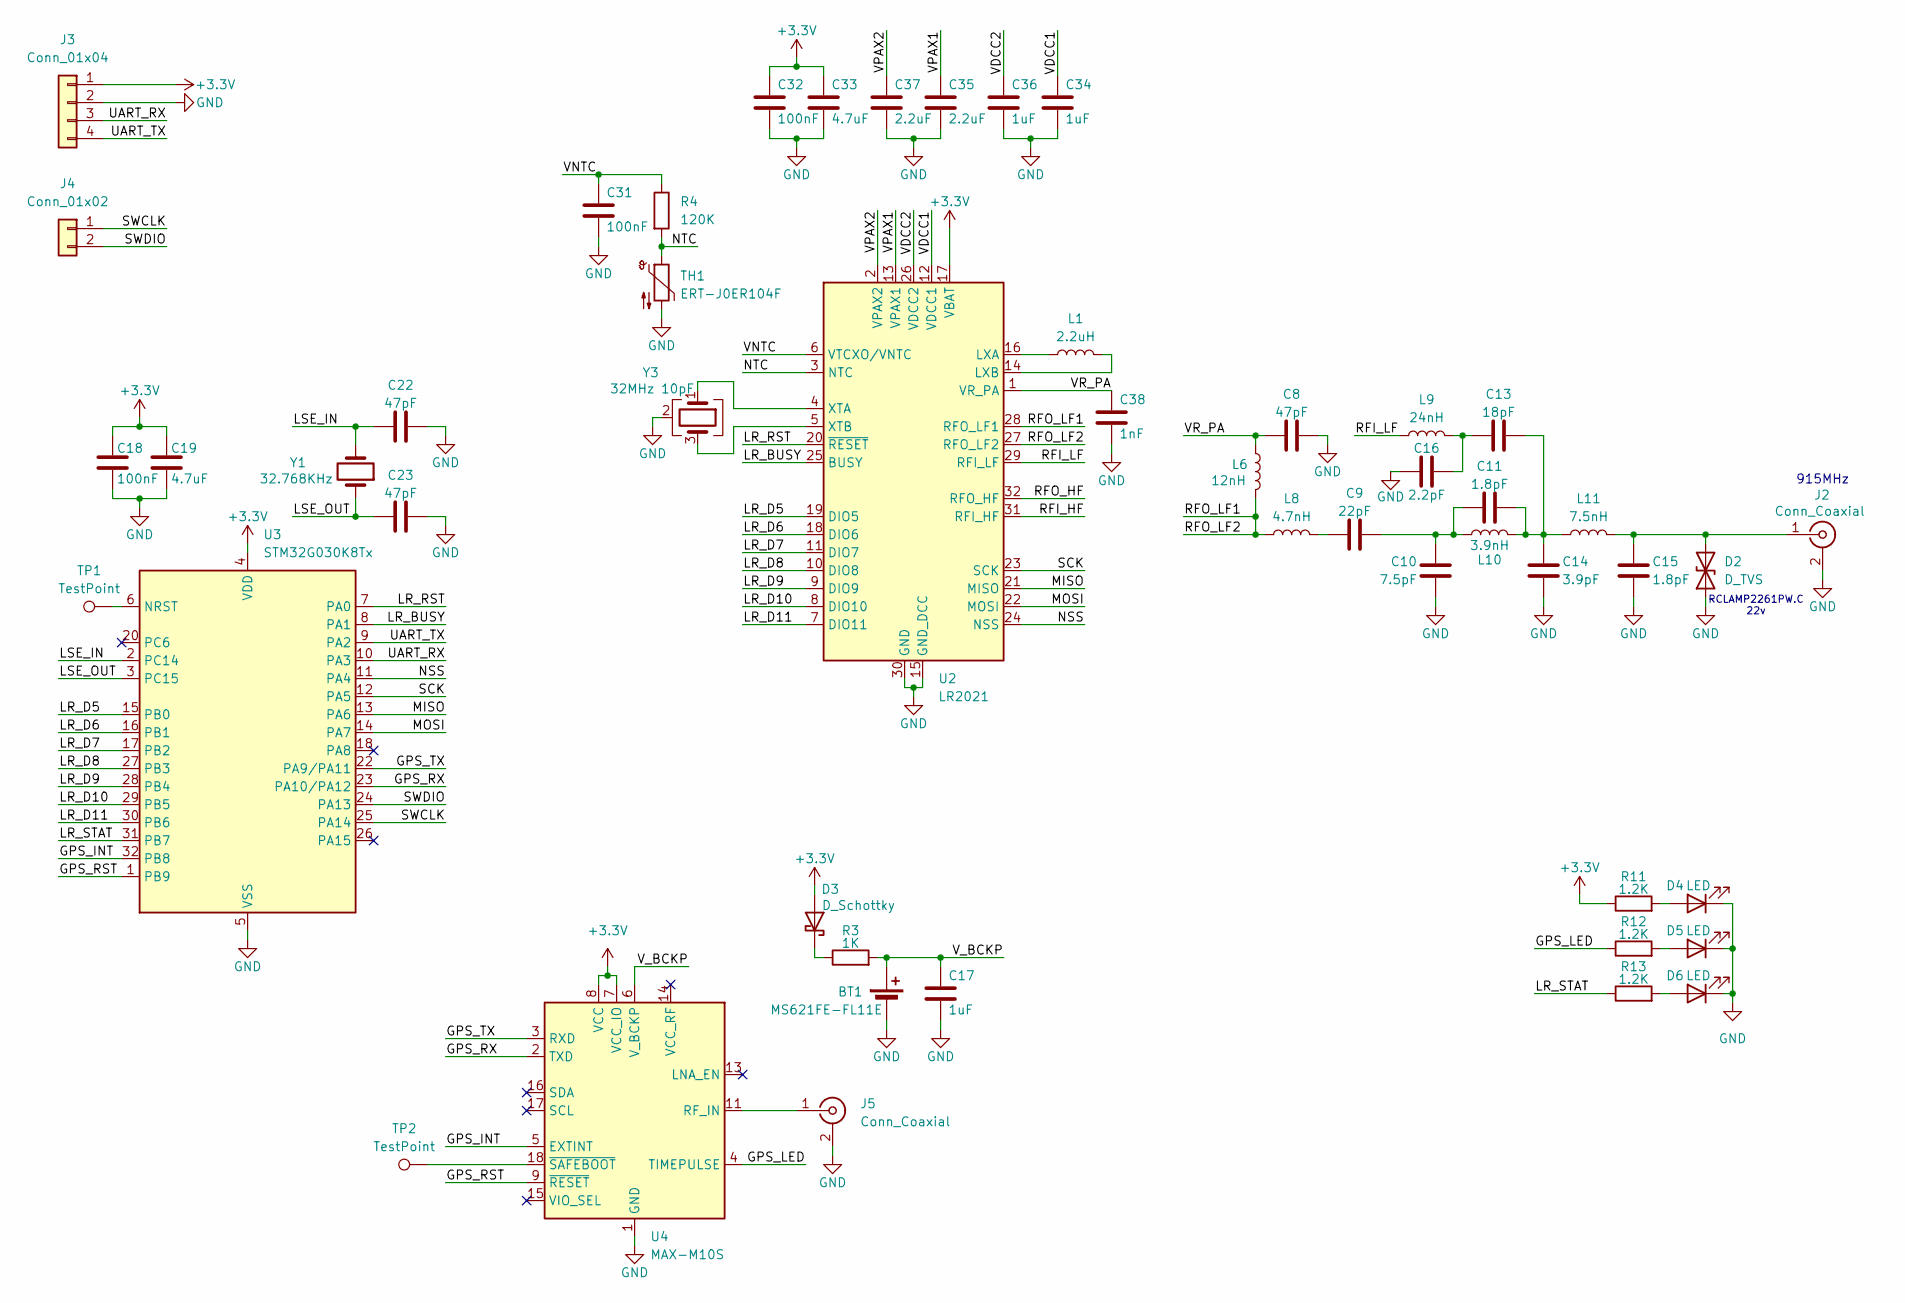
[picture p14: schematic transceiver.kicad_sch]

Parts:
BT1: MS621FE-FL11E; BAT_MS621FE-FL11E
C8, C22, C23: 47pF; C_0402_1005Metric
C9: 22pF; C_0402_1005Metric
C10: 7.5pF; C_0402_1005Metric
C11, C15: 1.8pF; C_0402_1005Metric
C13: 18pF; C_0402_1005Metric
C14: 3.9pF; C_0402_1005Metric
C16: 2.2pF; C_0402_1005Metric
C17: 1uF; C_0603_1608Metric
C18, C31, C32: 100nF; C_0402_1005Metric
C19, C33: 4.7uF; C_0603_1608Metric
C34, C36: 1uF; C_0402_1005Metric
C35, C37: 2.2uF; C_0402_1005Metric
C38: 1nF; C_0402_1005Metric
D2: D_TVS; D_0402_1005Metric
D3: D_Schottky; D_0603_1608Metric
D4, D5, D6: LED; LED_0603_1608Metric
J2, J5: Conn_Coaxial; U.FL_Molex_MCRF_73412-0110_Vertical
J3: Conn_01x04; PinHeader_1x04_P2.54mm_Vertical
J4: Conn_01x02; PinHeader_1x02_P2.54mm_Vertical
L1: 2.2uH; L_0603_1608Metric
L6: 12nH; L_0402_1005Metric
L8: 4.7nH; L_0402_1005Metric
L9: 24nH; L_0402_1005Metric
L10: 3.9nH; L_0402_1005Metric
L11: 7.5nH; L_0402_1005Metric
R3: 1K; R_0402_1005Metric
R4: 120K; R_0402_1005Metric
R11, R12, R13: 1.2K; R_0402_1005Metric
TH1: ERT-J0ER104F; R_0402_1005Metric
TP1, TP2: TestPoint; TestPoint_Pad_D1.0mm
U2: LR2021; QFN-32-1EP_7x7mm_P0.65mm_EP4.65x4.65mm
U3: STM32G030K8Tx; LQFP-32_7x7mm_P0.8mm
U4: MAX-M10S; ublox_MAX
Y1: 32.768KHz; Crystal_SMD_3215-2Pin_3.2x1.5mm
Y3: 32MHz 10pF; Crystal_SMD_2016-4Pin_2.0x1.6mm

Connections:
+3.3V: C18.1, C19.1, C32.1, C33.1, D3.2 (A), J3.1, R11.1, U2.17 (VBAT), U3.4 (VDD), U4.7 (VCC_IO), U4.8 (VCC)
/GPS_INT: U3.32 (PB8), U4.5 (EXTINT)
/GPS_LED: R12.1, U4.4 (TIMEPULSE)
/GPS_RST: U3.1 (PB9), U4.9 (~RESET)
/GPS_RX: U3.23 (PA10/PA12), U4.2 (TXD)
/GPS_TX: U3.22 (PA9/PA11), U4.3 (RXD)
/LR_BUSY: U2.25 (BUSY), U3.8 (PA1)
/LR_D5: U2.19 (DIO5), U3.15 (PB0)
/LR_D6: U2.18 (DIO6), U3.16 (PB1)
/LR_D7: U2.11 (DIO7), U3.17 (PB2)
/LR_D8: U2.10 (DIO8), U3.27 (PB3)
/LR_D9: U2.9 (DIO9), U3.28 (PB4)
/LR_D10: U2.8 (DIO10), U3.29 (PB5)
/LR_D11: U2.7 (DIO11), U3.30 (PB6)
/LR_RST: U2.20 (~RESET), U3.7 (PA0)
/LR_STAT: R13.1, U3.31 (PB7)
/LSE_IN: C22.2, U3.2 (PC14), Y1.2
/LSE_OUT: C23.2, U3.3 (PC15), Y1.1
/MISO: U2.21 (MISO), U3.13 (PA6)
/MOSI: U2.22 (MOSI), U3.14 (PA7)
/NSS: U2.24 (NSS), U3.11 (PA4)
/NTC: R4.2, TH1.1, U2.3 (NTC)
/RFI_HF: U2.31 (RFI_HF)
/RFI_LF: L9.1, U2.29 (RFI_LF)
/RFO_HF: U2.32 (RFO_HF)
/RFO_LF1: L6.2, L8.1, U2.27 (RFO_LF2), U2.28 (RFO_LF1)
/SCK: U2.23 (SCK), U3.12 (PA5)
/SWCLK: J4.1, U3.25 (PA14)
/SWDIO: J4.2, U3.24 (PA13)
/UART_RX: J3.3, U3.10 (PA3)
/UART_TX: J3.4, U3.9 (PA2)
/VDCC1: C34.1, U2.12 (VDCC1)
/VDCC2: C36.1, U2.26 (VDCC2)
/VNTC: C31.1, R4.1, U2.6 (VTCXO/VNTC)
/VPAX1: C35.1, U2.13 (VPAX1)
/VPAX2: C37.1, U2.2 (VPAX2)
/VR_PA: C8.1, C38.1, L6.1, U2.1 (VR_PA)
/V_BCKP: BT1.1 (+), C17.1, R3.2, U4.6 (V_BCKP)
GND: BT1.2 (-), C8.2, C10.2, C14.2, C15.2, C16.2, C17.2, C18.2, C19.2, C22.1, C23.1, C31.2, C32.2, C33.2, C34.2, C35.2, C36.2, C37.2, C38.2, D2.1 (A1), D4.1 (K), D5.1 (K), D6.1 (K), J2.2 (Ext), J3.2, J5.2 (Ext), TH1.2, U2.15 (GND_DCC), U2.30 (GND), U2.33 (GND), U3.5 (VSS), U4.1 (GND), U4.10 (GND), U4.12 (GND), Y3.2 (G), Y3.4 (G)
unnamed: C9.1, L8.2
unnamed: C9.2, C10.1, C11.1, L10.2
unnamed: C11.2, C13.2, C14.1, L10.1, L11.1
unnamed: C13.1, C16.1, L9.2
unnamed: C15.1, D2.2 (A2), J2.1 (In), L11.2
unnamed: D3.1 (K), R3.1
unnamed: D4.2 (A), R11.2
unnamed: D5.2 (A), R12.2
unnamed: D6.2 (A), R13.2
unnamed: J5.1 (In), U4.11 (RF_IN)
unnamed: L1.1, U2.16 (LXA)
unnamed: L1.2, U2.14 (LXB)
unnamed: U2.4 (XTA), Y3.1
unnamed: U2.5 (XTB), Y3.3
unnamed: TP1.1 (1_1), U3.6 (NRST)
unnamed: TP2.1 (1_1), U4.18 (~SAFEBOOT)

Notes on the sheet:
915MHz
RCLAMP2261PW.C 22v

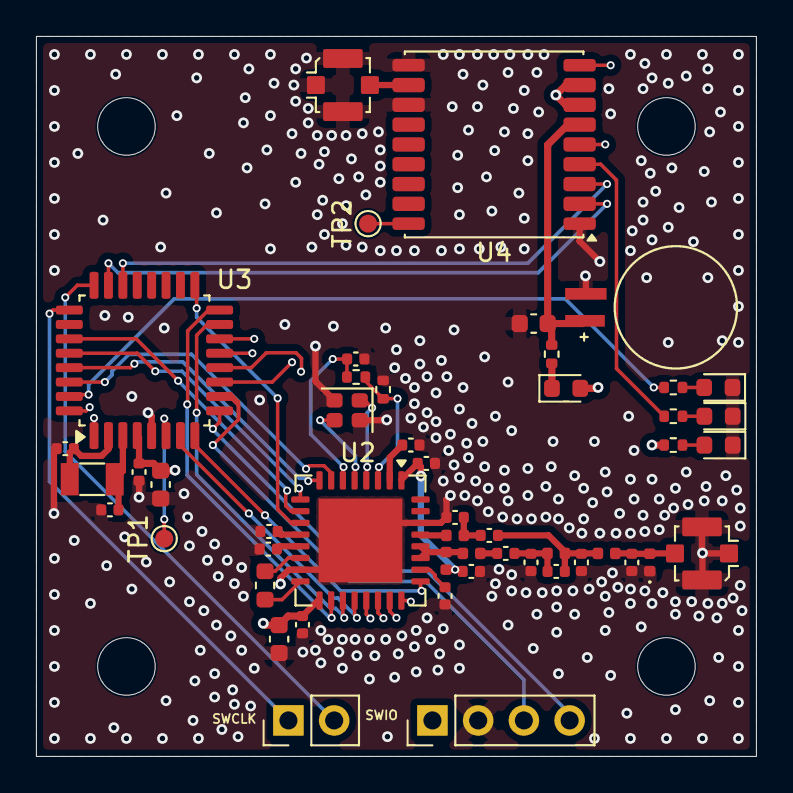
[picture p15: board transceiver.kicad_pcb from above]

Board: 4 copper layers, 40.0 x 40.0 mm, 50 parts (0 on the bottom side), 53 nets.

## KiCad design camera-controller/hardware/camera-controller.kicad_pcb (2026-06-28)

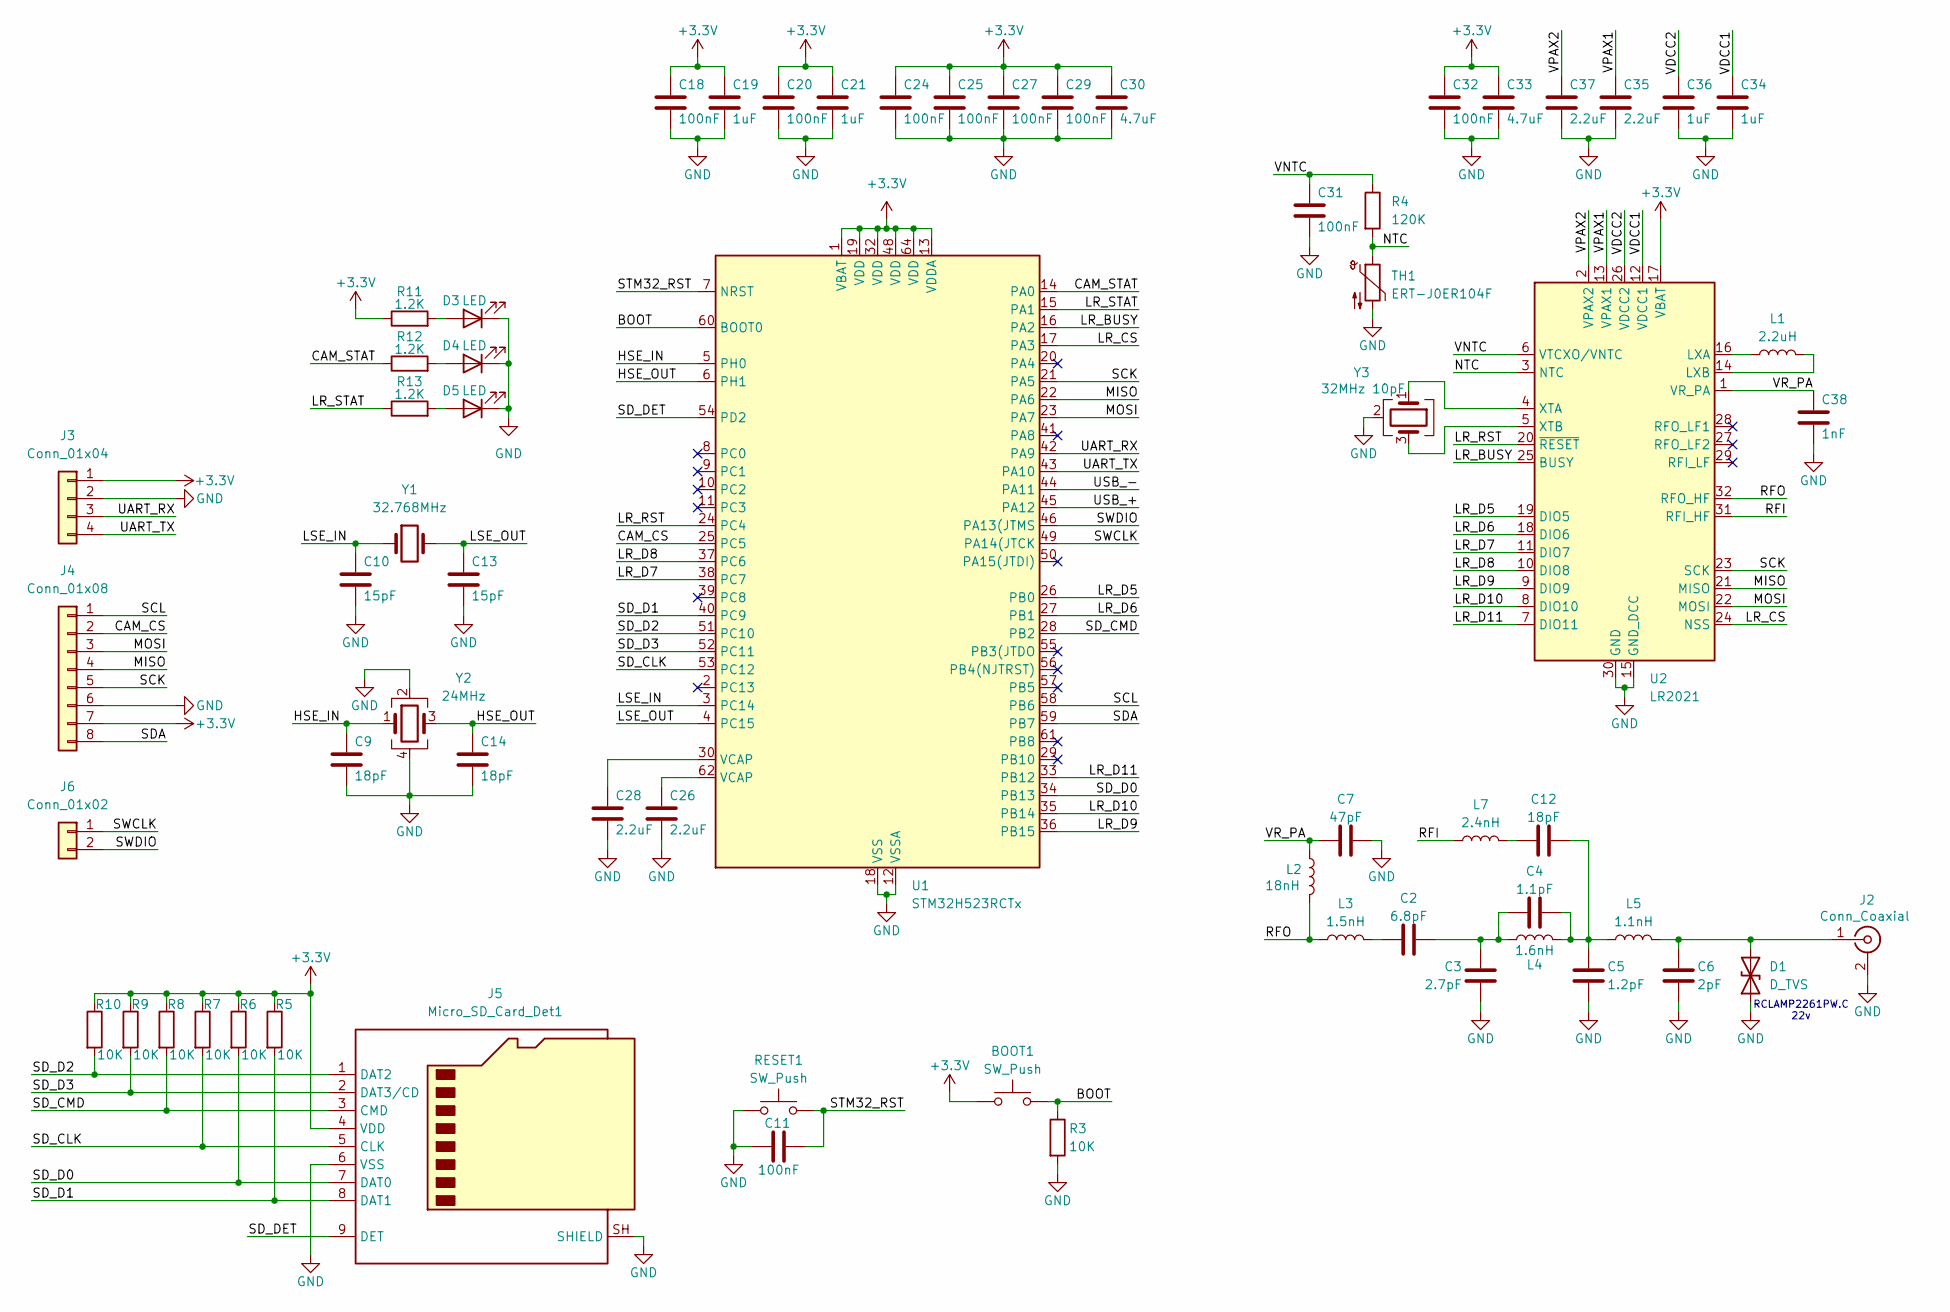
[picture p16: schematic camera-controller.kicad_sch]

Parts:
BOOT1: SW_Push; SW_Push_SPST_NO_Alps_SKRK
C2: 6.8pF; C_0402_1005Metric
C3: 2.7pF; C_0402_1005Metric
C4: 1.1pF; C_0402_1005Metric
C5: 1.2pF; C_0402_1005Metric
C6: 2pF; C_0402_1005Metric
C7: 47pF; C_0402_1005Metric
C9, C12, C14: 18pF; C_0402_1005Metric
C10, C13: 15pF; C_0402_1005Metric
C11, C18, C20, C24, C25, C27, C29, C31, C32: 100nF; C_0402_1005Metric
C19, C21, C34, C36: 1uF; C_0402_1005Metric
C26, C28, C35, C37: 2.2uF; C_0402_1005Metric
C30, C33: 4.7uF; C_0603_1608Metric
C38: 1nF; C_0402_1005Metric
D1: D_TVS; D_0402_1005Metric
D3, D4, D5: LED; LED_0603_1608Metric
J2: Conn_Coaxial; U.FL_Molex_MCRF_73412-0110_Vertical
J3: Conn_01x04; PinHeader_1x04_P2.54mm_Vertical
J4: Conn_01x08; PinHeader_1x08_P2.54mm_Vertical
J5: Micro_SD_Card_Det1; CUI_MSD-4-A
J6: Conn_01x02; PinHeader_1x02_P2.54mm_Vertical
L1: 2.2uH; L_0603_1608Metric
L2: 18nH; L_0402_1005Metric
L3: 1.5nH; L_0402_1005Metric
L4: 1.6nH; L_0402_1005Metric
L5: 1.1nH; L_0402_1005Metric
L7: 2.4nH; L_0402_1005Metric
R3, R5, R6, R7, R8, R9, R10: 10K; R_0402_1005Metric
R4: 120K; R_0402_1005Metric
R11, R12, R13: 1.2K; R_0402_1005Metric
RESET1: SW_Push; SW_Push_SPST_NO_Alps_SKRK
TH1: ERT-J0ER104F; R_0402_1005Metric
U1: STM32H523RCTx; LQFP-64_10x10mm_P0.5mm
U2: LR2021; QFN-32-1EP_7x7mm_P0.65mm_EP4.65x4.65mm
Y1: 32.768MHz; Crystal_SMD_3215-2Pin_3.2x1.5mm
Y2: 24MHz; Crystal_SMD_3225-4Pin_3.2x2.5mm
Y3: 32MHz 10pF; Crystal_SMD_2016-4Pin_2.0x1.6mm

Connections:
+3.3V: BOOT1.1, C18.1, C19.1, C20.1, C21.1, C24.1, C25.1, C27.1, C29.1, C30.1, C32.1, C33.1, J3.1, J4.7, J5.4 (VDD), R5.1, R6.1, R7.1, R8.1, R9.1, R10.1, R11.1, U1.1 (VBAT), U1.13 (VDDA), U1.19 (VDD), U1.32 (VDD), U1.48 (VDD), U1.64 (VDD), U2.17 (VBAT)
/BOOT: BOOT1.2, R3.1, U1.60 (BOOT0)
/CAM_CS: J4.2, U1.25 (PC5)
/CAM_STAT: R12.1, U1.14 (PA0)
/HSE_IN: C9.1, U1.5 (PH0), Y2.1
/HSE_OUT: C14.1, U1.6 (PH1), Y2.3
/LR_BUSY: U1.16 (PA2), U2.25 (BUSY)
/LR_CS: U1.17 (PA3), U2.24 (NSS)
/LR_D5: U1.26 (PB0), U2.19 (DIO5)
/LR_D6: U1.27 (PB1), U2.18 (DIO6)
/LR_D7: U1.38 (PC7), U2.11 (DIO7)
/LR_D8: U1.37 (PC6), U2.10 (DIO8)
/LR_D9: U1.36 (PB15), U2.9 (DIO9)
/LR_D10: U1.35 (PB14), U2.8 (DIO10)
/LR_D11: U1.33 (PB12), U2.7 (DIO11)
/LR_RST: U1.24 (PC4), U2.20 (~RESET)
/LR_STAT: R13.1, U1.15 (PA1)
/LSE_IN: C10.1, U1.3 (PC14), Y1.1
/LSE_OUT: C13.1, U1.4 (PC15), Y1.2
/MISO: J4.4, U1.22 (PA6), U2.21 (MISO)
/MOSI: J4.3, U1.23 (PA7), U2.22 (MOSI)
/NTC: R4.2, TH1.1, U2.3 (NTC)
/RFI: L7.1, U2.31 (RFI_HF)
/RFO: L2.2, L3.1, U2.32 (RFO_HF)
/SCK: J4.5, U1.21 (PA5), U2.23 (SCK)
/SCL: J4.1, U1.58 (PB6)
/SDA: J4.8, U1.59 (PB7)
/SD_CLK: J5.5 (CLK), R7.2, U1.53 (PC12)
/SD_CMD: J5.3 (CMD), R8.2, U1.28 (PB2)
/SD_D0: J5.7 (DAT0), R6.2, U1.34 (PB13)
/SD_D1: J5.8 (DAT1), R5.2, U1.40 (PC9)
/SD_D2: J5.1 (DAT2), R10.2, U1.51 (PC10)
/SD_D3: J5.2 (DAT3/CD), R9.2, U1.52 (PC11)
/SD_DET: J5.9 (DET), U1.54 (PD2)
/STM32_RST: C11.2, RESET1.2, U1.7 (NRST)
/SWCLK: J6.1, U1.49 (PA14(JTCK)
/SWDIO: J6.2, U1.46 (PA13(JTMS)
/UART_RX: J3.3, U1.42 (PA9)
/UART_TX: J3.4, U1.43 (PA10)
/USB_+: U1.45 (PA12)
/USB_-: U1.44 (PA11)
/VDCC1: C34.1, U2.12 (VDCC1)
/VDCC2: C36.1, U2.26 (VDCC2)
/VNTC: C31.1, R4.1, U2.6 (VTCXO/VNTC)
/VPAX1: C35.1, U2.13 (VPAX1)
/VPAX2: C37.1, U2.2 (VPAX2)
/VR_PA: C7.1, C38.1, L2.1, U2.1 (VR_PA)
GND: C3.2, C5.2, C6.2, C7.2, C9.2, C10.2, C11.1, C13.2, C14.2, C18.2, C19.2, C20.2, C21.2, C24.2, C25.2, C26.2, C27.2, C28.2, C29.2, C30.2, C31.2, C32.2, C33.2, C34.2, C35.2, C36.2, C37.2, C38.2, D1.1 (A1), D3.1 (K), D4.1 (K), D5.1 (K), J2.2 (Ext), J3.2, J4.6, J5.6 (VSS), J5.SH (SHIELD), R3.2, RESET1.1, TH1.2, U1.12 (VSSA), U1.18 (VSS), U1.31 (VSS), U1.47 (VSS), U1.63 (VSS), U2.15 (GND_DCC), U2.30 (GND), U2.33 (GND), Y2.2, Y2.4, Y3.2 (G), Y3.4 (G)
unnamed: C2.1, L3.2
unnamed: C2.2, C3.1, C4.1, L4.2
unnamed: C12.1, L7.2
unnamed: C4.2, C5.1, C12.2, L4.1, L5.1
unnamed: C26.1, U1.62 (VCAP)
unnamed: C28.1, U1.30 (VCAP)
unnamed: C6.1, D1.2 (A2), J2.1 (In), L5.2
unnamed: D3.2 (A), R11.2
unnamed: D4.2 (A), R12.2
unnamed: D5.2 (A), R13.2
unnamed: L1.1, U2.16 (LXA)
unnamed: L1.2, U2.14 (LXB)
unnamed: U2.4 (XTA), Y3.1
unnamed: U2.5 (XTB), Y3.3

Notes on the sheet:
RCLAMP2261PW.C 22v

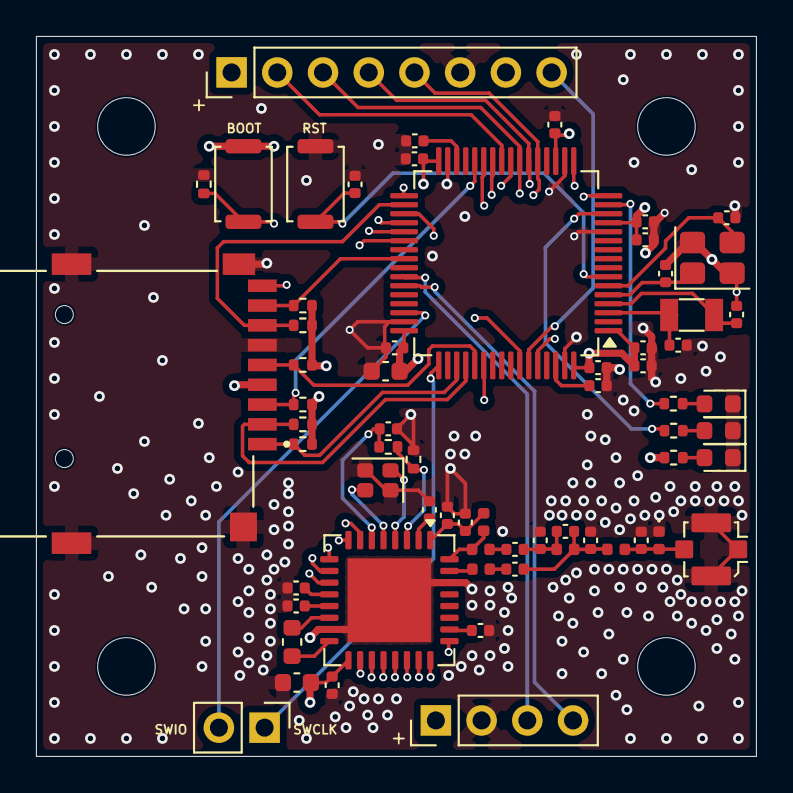
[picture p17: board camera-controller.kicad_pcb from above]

Board: 4 copper layers, 40.0 x 40.0 mm, 65 parts (0 on the bottom side), 60 nets.

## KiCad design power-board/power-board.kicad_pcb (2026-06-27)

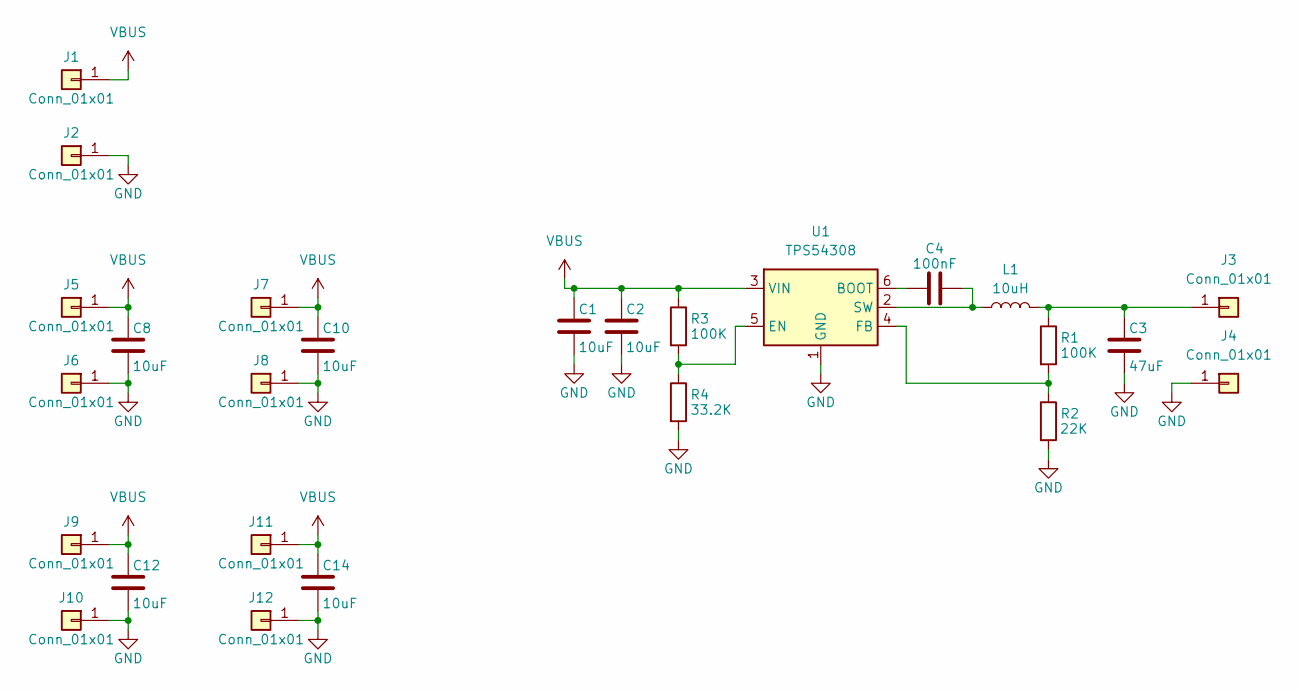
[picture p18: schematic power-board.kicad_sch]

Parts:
C1, C2, C8, C10, C12, C14: 10uF; C_1210_3225Metric
C3: 47uF; C_1210_3225Metric
C4: 100nF; C_0402_1005Metric
J1, J2, J3, J4, J5, J6, J7, J8, J9, J10, J11, J12: Conn_01x01; SolderWirePad_1x01_SMD_4x8mm
L1: 10uH; L_10.4x10.4_H4.8
R1, R3: 100K; R_0402_1005Metric
R2: 22K; R_0402_1005Metric
R4: 33.2K; R_0402_1005Metric
U1: TPS54308; SOT-23-6

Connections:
GND: C1.2, C2.2, C3.2, C8.2, C10.2, C12.2, C14.2, J2.1 (Pin_1_1), J4.1 (Pin_1_1), J6.1 (Pin_1_1), J8.1 (Pin_1_1), J10.1 (Pin_1_1), J12.1 (Pin_1_1), R2.2, R4.2, U1.1 (GND)
unnamed: C3.1, J3.1 (Pin_1_1), L1.2, R1.1
unnamed: C4.1, U1.6 (BOOT)
unnamed: R3.2, R4.1, U1.5 (EN)
unnamed: R1.2, R2.1, U1.4 (FB)
unnamed: C4.2, L1.1, U1.2 (SW)
VBUS: C1.1, C2.1, C8.1, C10.1, C12.1, C14.1, J1.1 (Pin_1_1), J5.1 (Pin_1_1), J7.1 (Pin_1_1), J9.1 (Pin_1_1), J11.1 (Pin_1_1), R3.1, U1.3 (VIN)

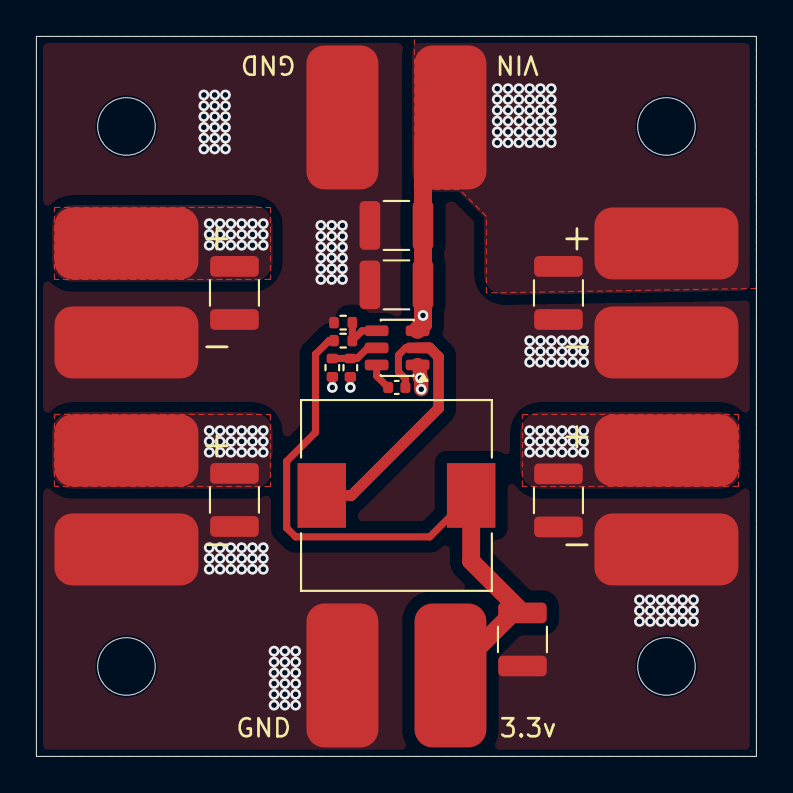
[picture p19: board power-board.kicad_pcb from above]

Board: 4 copper layers, 40.0 x 40.0 mm, 26 parts (0 on the bottom side), 7 nets.

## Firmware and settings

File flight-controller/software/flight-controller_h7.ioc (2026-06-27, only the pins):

Mcu.UserName=STM32H7A3RGTx
PA0.Signal=UART4_TX
PA1.Signal=UART4_RX
PA10.Signal=GPIO_Input
PA11.Signal=USB_OTG_HS_DM
PA12.Signal=USB_OTG_HS_DP
PA13.Signal=DEBUG_JTMS-SWDIO
PA14.Signal=DEBUG_JTCK-SWCLK
PA2.Signal=GPIO_Output
PA3.Signal=GPIO_Input
PA8.Signal=S_TIM1_CH1
PA9.Signal=S_TIM1_CH2
PB1.Signal=GPIO_Input
PB12.Signal=UART5_RX
PB13.Signal=UART5_TX
PB14.Signal=USART1_TX
PB15.Signal=USART1_RX
PB2.Signal=GPIO_Input
PB6.Signal=S_TIM4_CH1
PB7.Signal=S_TIM4_CH2
PB8.Signal=I2C1_SCL
PB9.Signal=I2C1_SDA
PC14-OSC32_IN.Signal=RCC_OSC32_IN
PC15-OSC32_OUT.Signal=RCC_OSC32_OUT
PC6.Signal=USART6_TX
PC7.Signal=USART6_RX
PH0-OSC_IN.Signal=RCC_OSC_IN
PH1-OSC_OUT.Signal=RCC_OSC_OUT

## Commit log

2026-04-09 init files
    [ESC.kicad_pcb, ESC.kicad_sch, camera-controller.kicad_pcb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]
2026-04-11 selected esc mosfet
    [ESC.kicad_sch]
2026-04-13 changed flight controller mcu
    [flight-controller.kicad_pcb, flight-controller.kicad_sch]
2026-04-13 added ground sensor
    [ground-sensor.kicad_pcb, ground-sensor.kicad_sch]
2026-04-13 worked on camera controller schematic
    [ESC.kicad_pcb, ESC.kicad_sch, camera-controller.kicad_pcb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]
2026-04-13 added micro sd card holder
    [camera-controller.kicad_sch]
2026-04-13 made camera controller schematic
    [camera-controller.kicad_sch]
2026-04-13 started pcb
    [camera-controller.kicad_pcb, camera-controller.kicad_sch]
2026-04-14 made camera controller pcb layout
    [camera-controller.kicad_pcb, camera-controller.kicad_sch]
2026-04-14 made transceiver schematic
    [transceiver.kicad_pcb, transceiver.kicad_sch]
2026-05-20 added mcu and gps
    [transceiver.kicad_sch]
2026-05-23 changed mcu and added gps
    [transceiver.kicad_sch]
2026-05-25 first draft of transceiver pcb
    [camera-controller.kicad_pcb, transceiver.kicad_pcb]
2026-05-25 touched up schematic
2026-05-31 updated board and started frame
    [Propeller_5_inch (1).stl, camera-controller.kicad_pcb, frame.FCStd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]
2026-06-01 working on frame
    [frame.FCStd, sketch.FCStd]
2026-06-07 added frame feet
    [feet.FCStd, frame.FCStd]
2026-06-08 prototyped frame
    [frame-Body.step, frame.FCStd]
2026-06-10 updated frame feet
    [feet-Body.step, feet.FCStd, frame.FCStd]
2026-06-15 testing pcb pannels
    [feet-Body.3mf, feet-Body.step, feet.FCStd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]
2026-06-25 finished camera controller pcb
    [camera-controller.kicad_pcb, camera-controller.kicad_sch]
2026-06-26 finished transceiver pcb
    [transceiver.kicad_sch]
2026-06-26 fixed via issues
    [transceiver.kicad_pcb]
2026-06-26 oops forgot to save
    [transceiver.kicad_pcb]
2026-06-27 finished flight controller pcb
    [flight-controller.kicad_pcb, flight-controller.kicad_sch]
2026-06-27 added power board
    [power-board.kicad_pcb, power-board.kicad_sch]
2026-06-28 added frame top and assembly
    [assembly.FCStd, board_model.FCStd, feet.FCStd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]
2026-06-28 optimized power trace
    [camera-controller.kicad_pcb]
2026-06-28 started production pcb
    [production-pcb.kicad_pcb]
2026-06-30 added production files
    [bom.csv, camera-controller.kicad_sch, designators.csv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]
2026-06-30 added frame image
